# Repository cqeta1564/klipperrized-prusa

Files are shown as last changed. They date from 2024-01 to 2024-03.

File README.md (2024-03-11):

"Buy Me A Coffee" (https://www.buymeacoffee.com/cqeta1564)
# Basic info
This project transforms the original Prusa i3 MK3S+ into a printer running Klipper. The user interface is Mainsail. This mod is safe unless you play with the config. This mod is also not permanent. More information on [how to get back](https://github.com/cqeta1564/klipperrized-prusa/blob/main/README.md#how-to-get-back-to-the-original-firmware).

What you will get from doing this modification to your printer. Faster prints, better quality, and quieter operations.

# Tutorial

## Hardware needed
- The best option is to use a Raspberry Pi Zero (2W preferred), but if you prefer Raspberry Pi 2/3/4/5 can also be used with a bit more work and a few more wires
- If using Raspberry Pi Zero, you'll need [male headers](https://amzn.to/3XND883) so it can mount directly to the Einsy board
- Micro-USB to USB-B (printer cable) or a micro-USB adapter if you already have a USB-B cable

## Pre-Check
- Get the Z offset value from your current firmware (Menu -> Calibration -> Z-offset)

## Installing Mainsail on your Raspberry Pi
1. Download [Pi Imager](https://downloads.raspberrypi.org/imager/imager_latest.exe), install it, and open it

2. 
	a. Select the right board that you are using

	b. Select "Choose OS" > "Other specific-purpose OS" > "3D Printing" > "Mainsail OS" > select the 32-bit version

 	c. Select "Choose Storage" > select the SD card that you want to flash

	d. Select "Next" > "Edit Settings"

	e. In "General" tick "Set username and password" and fill it out

	f. In "General" tick "Configure wireless LAN" if you plan on using wifi and fill it out

	g. In "General" tick "Set locale settings" and fill it out

	h. In "Services" tick "Enable SSH" and choose "Use password authentication"

	i. Click "Save" > "Yes"

3. For Pi Zero users, solder the headers onto the Pi per [Prusa's official instructions](https://help.prusa3d.com/en/article/raspberry-pi-zero-w-preparation-and-installation_2180), but do not plug it into the Einsy board yet

4. Power off your printer and plug in your Pi to the Einsy board per [Prusa's official instructions](https://help.prusa3d.com/en/article/raspberry-pi-zero-w-preparation-and-installation_2180), or power it with a micro USB

5. Power on your printer and navigate to "yourHostName".local/ or IP address of your Pi

6. Navigate to the "Machine" tab and scroll down to "Update Manager". If you see a lot of red buttons that say "invalid" or "error", then give the board 5 minutes and then reboot the board using the power button in the top right corner of the Mainsail interface

7. Navigate back to the update manager, and if the buttons are still red, then wait about 5 minutes. They will eventually populate. There will be a button at the bottom that says "Update All Components" Click this to update all packages to the latest

8. Reboot the Pi again

9. In the "Machine" tab, upload "printer.cfg" from my GitHub

## Flashing Einsy and Setting up Communications between Rpi and Einsy
1. Power down your Pi in Mainsail. If your Pi is plugged into your printer, power that down too and remove the Pi. Connect the USB power source to the micro-USB port on the furthest edge of the board labelled "PWR IN". Plug your micro-USB to USB-b cable in the centre micro-USB port labelled "USB", and then plug the other end into your Einsy mainboard. Turn your printer on if it isn't already.

2. To flash Klipper onto your Einsy

a. Download [Putty](https://www.chiark.greenend.org.uk/~sgtatham/putty/latest.html) and connect to your Pi. Enter the following commands  

   ```yml
   cd ~/klipper/
   make menuconfig   
   ```
   
Compile the firmware for "AVR" "atmega2560". To connect your Pi Zero over serial, select "Enable extra low-level configuration options" and select **UART1** (the RasPi serial) or **UART0** when you plan to connect via the USB.
   Press "q" and exit

   ```yml
   make
   ```

b. find the port for the USB cable

   ```yml
   ls /dev/serial/by-id/*
   ```

Putty will return something like "/dev/serial/by-id/usb-1a86_USB2.0-Serial-if00-port0" or "/dev/serial/by-id/usb-Prusa_Research__prusa3d.com__Original_Prusa_i3_MK3_CZPX4820X004XK35533-if00"
	
Copy this line and replace the corresponding line in the code below. Then run those commands in Putty
	
   ```yml
   sudo service klipper stop
   make flash FLASH_DEVICE=/dev/serial/by-id/usb-1a86_USB2.0-Serial-if00-port0
   sudo service klipper start
   ```

3. Restart the printer by turning the power supply off and on againg
   
4. Ready to print

## How to use PrusaSlicer profiles
You can download profile.ini bundle but be aware that it wont be up to date with newest PrusaSlicer configs. You can also configure your own profile by this tutorial below:

Use profile for Original Prusa MK3.5 Input Shaper with "Print Settings" > "Advanced"  > "Arc fitting" turned off and set "G-code resolution to 0.006. In "Printer Settings" > "General" set "G-code flavor" to "Klipper" and "G-code thumbnail" to "64x64/PNG, 400x300/PNG" and turn off "Supports binary G-code". In "Custom G-code" set "Start G-code" to this: 
```yml
G90 ; use absolute coordinates
M83 ; extruder relative mode

M140 S[first_layer_bed_temperature] ; set bed temp
M104 S170 ; set extruder temp for bed leveling
M109 S170 ; wait for temp
M190 S[first_layer_bed_temperature] ; wait for bed temp

G28 ; home all

BED_MESH_CALIBRATE AREA_START={first_layer_print_min[0]},{first_layer_print_min[1]} AREA_END={first_layer_print_max[0]},{first_layer_print_max[1]}

; prepare for purge
M104 S{first_layer_temperature[0]}
G0 X0 Y-4 Z15 F4800 ; move away and ready for the purge
M109 S{first_layer_temperature[0]}

; Extrude purge line

G92 E0 ; reset extruder position
G0 E7 X15 Z0.2 F500 ; purge
G0 X25 E4 F500 ; purge
G0 X35 E4 F650 ; purge
G0 X45 E4 F800 ; purge
G0 X{45 + 3} Z0.05 F8000 ; wipe, move close to the bed
G0 X{45 + 3 * 2} Z0.2 F8000 ; wipe, move quickly away from the bed

G92 E0
M221 S100 ; reset flow to 100%
```

And "End G-code" to this:
```yml
{if layer_z < max_print_height}G1 Z{z_offset+min(layer_z+1, max_print_height)} F720 ; Move print head up{endif}
M104 S0 ; turn off temperature
M140 S0 ; turn off heatbed
M107 ; turn off fan
G1 X241 Y201 F3600 ; park
{if layer_z < max_print_height}G1 Z{z_offset+min(layer_z+23, max_print_height)} F300 ; Move print head up{endif}
G4 ; wait
M572 S0 ; reset PA
M84 X Y E ; disable motors
; max_layer_z = [max_layer_z]
```

And "Before layer change G-code" to this:
```yml
;BEFORE_LAYER_CHANGE
G92 E0.0
;[layer_z]
M201 X{interpolate_table(extruded_weight_total, (0,4000), (1400,2500), (10000,2500))} Y{interpolate_table(extruded_weight_total, (0,4000), (1400,2500), (10000,2500))}
```

That is all for the fast mk3.5 profile or you can just use slow and old profile for Original Prusa i3 MK3S & MK3S+ with these modifications:

In "Printer Settings" > "General" set "G-code flavor" to "Klipper" and "G-code thumbnail" to "64x64/PNG, 400x300/PNG". In "Custom G-code" set "Start G-code" to this: 

```yml
G90 ; use absolute coordinates
M83 ; extruder relative mode
M140 S[first_layer_bed_temperature] ; set bed temp
M190 S[first_layer_bed_temperature] ; wait for bed temp
G28 W ; home all without mesh bed level
BED_MESH_CALIBRATE AREA_START={first_layer_print_min[0]},{first_layer_print_min[1]} AREA_END={first_layer_print_max[0]},{first_layer_print_max[1]}
{if filament_settings_id[initial_tool]=~/.*Prusament PA11.*/}
G1 Z0.3 F720
G1 Y-3 F1000 ; go outside print area
M104 S[first_layer_temperature] ; set extruder temp
M109 S[first_layer_temperature] ; wait for extruder temp
G92 E0
G1 X60 E9 F1000 ; intro line
G1 X100 E9 F1000 ; intro line
{else}
G1 Z0.2 F720
G1 Y-3 F1000 ; go outside print area
M104 S[first_layer_temperature] ; set extruder temp
M109 S[first_layer_temperature] ; wait for extruder temp
G92 E0
G1 X60 E9 F1000 ; intro line
G1 X100 E12.5 F1000 ; intro line
{endif}
G92 E0
M221 S{if layer_height<0.075}100{else}95{endif}
```

## Optional things that are nice to have 

### Klipper mesh on the print area only
Just download my PrusaSlicer configuration package and use the provided printer profile to use this feature. The Klipper configuration is already set up with this feature.

### Recalibrating input shaper
More info is comming. In the meantime, here is oficial klipper guide: [Recalibrating input shaper](https://www.klipper3d.org/Resonance_Compensation.html) just for your printer using [ADXl345](https://amzn.to/3XMmTZa)

## How to get back to the original firmware
Just reflash the Einsy with the original firmware using PrusaSlicer, just like you would when upgrading it. You will not lose print statistics because they are stored in memory that is not used by Klipper.

## Sources
- Tutorial: https://github.com/Fail-Fast-V0/klipper-prusa-mk3s/
- The file from which my configuration is based on: https://github.com/tillin9/klipper/blob/patch-2/config/printer-prusa-mk3s-2021.cfg
- Another good configuration: https://lab4450.com/latest-projects/revive-your-prusa-mk3s-with-klipper-2-5-compile-and-flash-klipper/
- Klipper mesh on the print area only install guide: https://gist.github.com/ChipCE/95fdbd3c2f3a064397f9610f915f7d02

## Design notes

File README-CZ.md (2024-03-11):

"Buy Me A Coffee" (https://www.buymeacoffee.com/cqeta1564)
# Základní informace
Tento projekt přeměňuje původní tiskárnu Prusa i3 MK3S+ na tiskárnu se systémem Klipper. Uživatelské rozhraní je Mainsail. Tato modifikace je bezpečná, pokud si nebudete hrát s konfigurací. Tato modifikace také není trvalá. Více informací najdete na stránce [jak se dostat zpět](https://github.com/cqeta1564/klipperrized-prusa/blob/main/README-CZ.md#jak-se-vrátit-k-původnímu-firmwaru).

Co touto úpravou tiskárny získáte. Rychlejší výtisky, lepší kvalitu a tišší provoz.

# Tutorial

## Potřebný hardware
- Nejlepší možností je použít Raspberry Pi Zero (nejlépe 2W), ale pokud dáváte přednost Raspberry Pi 2/3/4/5, lze také použít s trochou více práce a několika dalšími dráty.
- Pokud používáte Raspberry Pi Zero, budete potřebovat [samčí hlavičky](https://amzn.to/3XND883), abyste jej mohli připojit přímo k desce Einsy.
- Micro-USB na USB-B (kabel k tiskárně) nebo adaptér micro-USB, pokud již máte kabel USB-B.

## Pre-Check
- Zjistěte hodnotu posunu Z z aktuálního firmwaru (Menu -> Kalibrace -> Posun Z).

## Instalace systému Mainsail do počítače Raspberry Pi
1. Stáhněte si [Pi Imager](https://downloads.raspberrypi.org/imager/imager_latest.exe), nainstalujte jej a otevřete.

2. 
	a. Vyberte správnou desku, kterou používáte

	b. Vyberte "Zvolit OS" > "Jiný OS pro konkrétní účely" > "3D tisk" > "Mainsail OS" > vyberte 32bitovou verzi.

	 c. Vyberte "Choose Storage" > vyberte kartu SD, kterou chcete flashovat.

	d. Vyberte "Další" > "Upravit nastavení".

	e. V části "Obecné" zaškrtněte políčko "Nastavit uživatelské jméno a heslo" a vyplňte je.

	f. V části "Obecné" zaškrtněte políčko "Konfigurace bezdrátové sítě LAN", pokud plánujete používat wifi, a vyplňte jej.

	g. V části "Obecné" zaškrtněte políčko "Nastavení místního jazyka" a vyplňte jej.

	h. V části "Služby" zaškrtněte políčko "Povolit SSH" a vyberte možnost "Použít ověřování heslem".

	i. Klikněte na "Uložit" > "Ano".

3. Uživatelé Pi Zero připájejte hlavičky na Pi podle [oficiálního návodu Prusa](https://help.prusa3d.com/en/article/raspberry-pi-zero-w-preparation-and-installation_2180), ale ještě je nezapojujte do desky Einsy.

4. Vypněte tiskárnu a připojte počítač Pi k desce Einsy podle [oficiálního návodu Prusa](https://help.prusa3d.com/en/article/raspberry-pi-zero-w-preparation-and-installation_2180) nebo jej napájejte pomocí micro USB.

5. Zapněte tiskárnu a přejděte na adresu "yourHostName".local/ nebo IP adresu vašeho počítače Pi.

6. Přejděte na kartu "Stroj" a přejděte dolů na položku "Správce aktualizací". Pokud se zobrazí spousta červených tlačítek s nápisem "invalid" (neplatné) nebo "error" (chyba), dejte desce 5 minut a poté ji restartujte pomocí tlačítka napájení v pravém horním rohu rozhraní programu Mainsail.

7. Přejděte zpět do správce aktualizací, a pokud jsou tlačítka stále červená, počkejte asi 5 minut. Nakonec se vyplní. V dolní části bude tlačítko s nápisem "Aktualizovat všechny součásti" Kliknutím na něj aktualizujete všechny balíčky na nejnovější verzi.

8. Znovu restartujte počítač Pi

9. Na kartě "Machine" nahrajte soubor "printer.cfg" z mého GitHubu.

## Programování Einsy a nastavení komunikace mezi Rpi a Einsy
1. Vypněte počítač Pi v hlavní plachtě. Pokud je počítač Pi připojen k tiskárně, vypněte i ji a vyjměte počítač Pi. Připojte zdroj napájení USB k portu micro-USB na nejvzdálenějším okraji desky označeném "PWR IN". Zapojte kabel micro-USB na USB-b do prostředního portu micro-USB označeného "USB" a druhý konec připojte k základní desce Einsy. Zapněte tiskárnu, pokud ještě není zapnutá.

2. Flashování softwaru Klipper na zařízení Einsy

a. Stáhněte si [Putty](https://www.chiark.greenend.org.uk/~sgtatham/putty/latest.html) a připojte se k počítači Pi. Zadejte následující příkazy  

   ```yml
   cd ~/klipper/
   make menuconfig   
   ```
   
Zkompilujte firmware pro "AVR" "atmega2560". Chcete-li připojit Pi Zero přes sériové rozhraní, vyberte možnost "Enable extra low-level configuration options" (Povolit další nízkoúrovňové konfigurační možnosti) a vyberte **UART1** (sériové rozhraní RasPi) nebo **UART0**, pokud se plánujete připojit přes USB.
   Stiskněte tlačítko "q" a ukončete

   ```yml
   make
   ```

b. najděte port pro kabel USB

   ```yml
   ls /dev/serial/by-id/*
   ```

Putty vrátí něco jako "/dev/serial/by-id/usb-1a86_USB2.0-Serial-if00-port0" nebo "/dev/serial/by-id/usb-Prusa_Research__prusa3d.com__Original_Prusa_i3_MK3_CZPX4820X004XK35533-if00".
	
Zkopírujte tento řádek a nahraďte jím odpovídající řádek v níže uvedeném kódu. Poté spusťte tyto příkazy v programu Putty
	
   ```yml
   sudo service klipper stop
   make flash FLASH_DEVICE=/dev/serial/by-id/usb-1a86_USB2.0-Serial-if00-port0
   sudo service klipper start
   ```

3. Restartujte tiskárnu vypnutím a opětovným zapnutím napájení.
   
4. Připraveno k tisku

## Jak používat profily PrusaSlicer
Můžete si stáhnout balíček profile.ini, ale počítejte s tím, že nebude aktuální s nejnovější konfigurací PrusaSliceru. Můžete si také nakonfigurovat vlastní profil podle tohoto návodu níže:

Použijte profil Original Prusa MK3.5 Input Shaper s vypnutým "Nastavení tisku" > "Pokročilé" > "Přizpůsobení obloukem" a nastavte "G-code rozlišení" na 0.006. V "Nastavení tiskárny" > "Obecné" nastavte "Druh G-code" na "Klipper" a "Náhledy G-codu" na "64x64/PNG, 400x300/PNG" a vypněte "Podpora binárního G-code". V části "Vlastní G-code" nastavte "Začátek G-code" na tuto hodnotu: 
```yml
G90 ; use absolute coordinates
M83 ; extruder relative mode

M140 S[first_layer_bed_temperature] ; set bed temp
M104 S170 ; set extruder temp for bed leveling
M109 S170 ; wait for temp
M190 S[first_layer_bed_temperature] ; wait for bed temp

G28 ; home all

BED_MESH_CALIBRATE AREA_START={first_layer_print_min[0]},{first_layer_print_min[1]} AREA_END={first_layer_print_max[0]},{first_layer_print_max[1]}

; prepare for purge
M104 S{first_layer_temperature[0]}
G0 X0 Y-4 Z15 F4800 ; move away and ready for the purge
M109 S{first_layer_temperature[0]}

; Extrude purge line

G92 E0 ; reset extruder position
G0 E7 X15 Z0.2 F500 ; purge
G0 X25 E4 F500 ; purge
G0 X35 E4 F650 ; purge
G0 X45 E4 F800 ; purge
G0 X{45 + 3} Z0.05 F8000 ; wipe, move close to the bed
G0 X{45 + 3 * 2} Z0.2 F8000 ; wipe, move quickly away from the bed

G92 E0
M221 S100 ; reset flow to 100%
```

A "Konec G-code" na tuto:
```yml
{if layer_z < max_print_height}G1 Z{z_offset+min(layer_z+1, max_print_height)} F720 ; Move print head up{endif}
M104 S0 ; turn off temperature
M140 S0 ; turn off heatbed
M107 ; turn off fan
G1 X241 Y201 F3600 ; park
{if layer_z < max_print_height}G1 Z{z_offset+min(layer_z+23, max_print_height)} F300 ; Move print head up{endif}
G4 ; wait
M572 S0 ; reset PA
M84 X Y E ; disable motors
; max_layer_z = [max_layer_z]
```

A "G-code před změnou vrstvy" na toto:
```yml
;BEFORE_LAYER_CHANGE
G92 E0.0
;[layer_z]
M201 X{interpolate_table(extruded_weight_total, (0,4000), (1400,2500), (10000,2500))} Y{interpolate_table(extruded_weight_total, (0,4000), (1400,2500), (10000,2500))}
```

To je vše pro rychlý profil mk3.5 nebo můžete použít jen pomalý a starý profil pro Original Prusa i3 MK3S & MK3S+ s těmito úpravami:

V "Nastavení tiskárny" > "Obecné" nastavte "Druh G-code" na "Klipper" a "Náhledy G-codu" na "64x64/PNG, 400x300/PNG". V části "Vlastní G-code" nastavte "Začátek G-code" na tuto hodnotu: 
```yml
G90 ; use absolute coordinates
M83 ; extruder relative mode
M140 S[first_layer_bed_temperature] ; set bed temp
M190 S[first_layer_bed_temperature] ; wait for bed temp
G28 W ; home all without mesh bed level
BED_MESH_CALIBRATE AREA_START={first_layer_print_min[0]},{first_layer_print_min[1]} AREA_END={first_layer_print_max[0]},{first_layer_print_max[1]}
{if filament_settings_id[initial_tool]=~/.*Prusament PA11.*/}
G1 Z0.3 F720
G1 Y-3 F1000 ; go outside print area
M104 S[first_layer_temperature] ; set extruder temp
M109 S[first_layer_temperature] ; wait for extruder temp
G92 E0
G1 X60 E9 F1000 ; intro line
G1 X100 E9 F1000 ; intro line
{else}
G1 Z0.2 F720
G1 Y-3 F1000 ; go outside print area
M104 S[first_layer_temperature] ; set extruder temp
M109 S[first_layer_temperature] ; wait for extruder temp
G92 E0
G1 X60 E9 F1000 ; intro line
G1 X100 E12.5 F1000 ; intro line
{endif}
G92 E0
M221 S{if layer_height<0.075}100{else}95{endif}
```

## Nepovinné věci, které je dobré mít

### Klipper mesh pouze v oblasti tisku
Stačí si stáhnout můj konfigurační balíček PrusaSlicer a použít dodaný profil tiskárny, abyste mohli tuto funkci používat. Konfigurace Klipperu je již s touto funkcí nastavena.

### Překalibrování input shaperu
Další informace se chystají. Mezitím je zde oficiální průvodce klipperem: [Překalibrování input shaperu](https://www.klipper3d.org/Resonance_Compensation.html) právě pro vaši tiskárnu pomocí [ADXl345](https://amzn.to/3XMmTZa)

## Jak se vrátit k původnímu firmwaru
Stačí přeflashovat Einsy původním firmwarem pomocí PrusaSlicer, stejně jako při aktualizaci. O tiskové statistiky nepřijdete, protože jsou uloženy v paměti, kterou Klipper nepoužívá.

## Zdroje
- Výukový kurz: https://github.com/Fail-Fast-V0/klipper-prusa-mk3s/
- Soubor, ze kterého vychází moje konfigurace: https://github.com/tillin9/klipper/blob/patch-2/config/printer-prusa-mk3s-2021.cfg
- Další dobrá konfigurace: https://lab4450.com/latest-projects/revive-your-prusa-mk3s-with-klipper-2-5-compile-and-flash-klipper/
- Síťka Klipper pouze v oblasti tisku Návod k instalaci: https://gist.github.com/ChipCE/95fdbd3c2f3a064397f9610f915f7d02

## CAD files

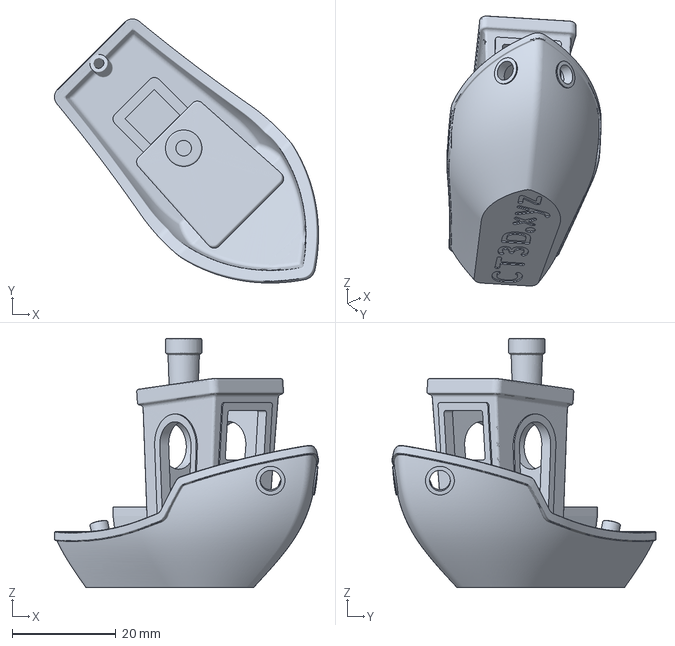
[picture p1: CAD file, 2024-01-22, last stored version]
G2G3TURNEDOFF3dbenchy.3mf
50.8 x 50.8 x 48.0 mm

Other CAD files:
FASTEST3dbenchy.3mf

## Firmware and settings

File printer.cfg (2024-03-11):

# This file contains pin mappings and reasonable defaults for Prusa i3 MK3S
# printers. It will work with MK3 (non-S) by selecting the alternative filament
# sensor. References to common community mods are included as well.
#
# Note: The Einsy boards sold by Prusa have defective firmware on the
# usb-to-serial chip that makes the boards unusable with Klipper through USB.
# While flashing Klipper firmware must be done over USB, the board can be used
# via serial with no additional modification.


# ================================
# =            SENSORS           =
# ================================
[temperature_sensor PC]
sensor_type: temperature_host
min_temp: 10
max_temp: 80

[temperature_sensor einsy_board]
sensor_pin: PF6
sensor_type: TDK NTCG104LH104JT1
min_temp: -10
max_temp: 70

#[temperature_sensor enclosure_temp]
#sensor_type: BME280
#i2c_mcu: host
#min_temp: -20
#max_temp: 120

#[adxl345]
#cs_pin: host:PB2

#[resonance_tester]
#accel_chip: adxl345
#probe_points:
#    125, 105, 20  # an example

[probe]
pin: PB4
x_offset: 24
y_offset: 5
#z_offset: 0
speed: 10.0
samples: 3 #Sampling, primarily for bed mesh. 3 is fine for normal PINDA probes.
samples_result: average
#sample_retract_dist: 1.0 #zkopirovano z druhyho configu, neni za potrebi, ale muze se hodit


# ================================
# =           STEPPERS           =
# ================================
[input_shaper]
shaper_freq_x: 58.0         #61.4  38.6  55.2  53.4      52.6
shaper_freq_y: 64.8         #39.2  44.4  33.6  57.6      56.8
shaper_type_x: ei           #zv    mzv   ei    2hump_ei  3hump_ei
shaper_type_y: 2hump_ei     #zv    mzv   ei    2hump_ei  3hump_ei

[stepper_x]
step_pin: PC0
dir_pin: !PL0
enable_pin: !PA7
#Step distances for common configurations, 16 tooth and 1.8 degree is Prusa.stock, but many people have 0.9 degree steppers to remove VFAs.
#step_distance: .01 #16 pin tooth wheel, 1.8 degree stepper.
#step_distance: .0125 #20 tooth drive wheel, 1.8 degree stepper.
#step_distance: 0.00625 #20 tooth drive wheel. 0.9 degree stepper.
#step_distance: .005 #16 tooth drive wheel, 0.9 degree stepper.
endstop_pin: tmc2130_stepper_x:virtual_endstop
position_endstop: 0
position_max: 250
homing_speed: 50
homing_retract_dist: 0
rotation_distance: 32
microsteps: 16

[tmc2130 stepper_x]
cs_pin: PG0
interpolate: True
run_current: .281738 #.281738
hold_current: .281738 #.281738
sense_resistor: 0.220
diag1_pin: !PK2
driver_IHOLDDELAY: 8
driver_TPOWERDOWN: 0
driver_TBL: 2
driver_TOFF: 3
driver_HEND: 1
driver_HSTRT: 5
driver_PWM_FREQ: 2
driver_PWM_GRAD: 2
driver_PWM_AMPL: 230
driver_PWM_AUTOSCALE: True
driver_SGT: 3

[stepper_y]
step_pin: PC1
dir_pin: PL1
enable_pin: !PA6
#Step distances for common configurations, 16 tooth and 1.8 degree is Prusa.stock, but many people have 0.9 degree steppers to remove VFAs.
#step_distance: .01 #16 pin tooth wheel, 1.8 degree stepper.
#step_distance: .0125 #20 tooth drive wheel, 1.8 degree stepper.
#step_distance: 0.00625 #20 tooth drive wheel. 0.9 degree stepper.
#step_distance: .005 #16 tooth drive wheel, 0.9 degree stepper.
endstop_pin: tmc2130_stepper_y:virtual_endstop
position_endstop: -4
position_max: 210
position_min: -4
homing_speed: 50
homing_retract_dist: 0
rotation_distance: 32
microsteps: 16

[tmc2130 stepper_y]
cs_pin: PG2
interpolate: True
run_current: .3480291 #.281738
hold_current: .3480291 #.281738
#Run at the same current as X-axis for lower noise, and to keep steppers cooler.
#This should work, but if Y starts skipping steps, you may need to bump up to Prusa stock.
#run_current: .3480291
#hold_current: .3480291
sense_resistor: 0.220
diag1_pin: !PK7
driver_IHOLDDELAY: 8
driver_TPOWERDOWN: 0
driver_TBL: 2
driver_TOFF: 3
driver_HEND: 1
driver_HSTRT: 5
driver_PWM_FREQ: 2
driver_PWM_GRAD: 2
#driver_PWM_AMPL: 235
driver_PWM_AMPL: 230
driver_PWM_AUTOSCALE: True
driver_SGT: 3

[stepper_z]
step_pin: PC2
dir_pin: !PL2
enable_pin: !PA5
#step_distance: .0025
endstop_pin: probe:z_virtual_endstop
#Please update the Z height in the Tram_Z macro below.
position_max: 200 #This is the MK3S default.
#position_max: 210 #Use this for a stock MK3 non-S, BMG, or Bear extruders for the MK3S.
position_min: -2
homing_speed: 13.333
rotation_distance: 8
microsteps: 16

[tmc2130 stepper_z]
cs_pin: PK5
interpolate: True
run_current: .53033
hold_current: .53033
sense_resistor: 0.220
diag1_pin: !PK6
driver_IHOLDDELAY: 8
driver_TPOWERDOWN: 0
driver_TBL: 2
driver_TOFF: 3
driver_HEND: 1
driver_HSTRT: 5
driver_PWM_FREQ: 2
driver_PWM_GRAD: 4
driver_PWM_AMPL: 200
driver_PWM_AUTOSCALE: True
driver_SGT: 4

[extruder]
step_pin: PC3
dir_pin: PL6
enable_pin: !PA4
#step_distance: .0035714 #Stock Prusa or Bear extruder.
#step_distance: .0012048 #BMG or other 3:1 ratio extruder.
nozzle_diameter: 0.400
filament_diameter: 1.750
# The max extrude cross section is increased for the purge line, but in theory
# its probably a bad idea to have it this large, as its purpose is to catch
# poorly sliced objects that extrude too much for small moves.
max_extrude_cross_section: 500.0
# Allows to load filament and purge up to 500mm
max_extrude_only_distance: 500.0
max_extrude_only_velocity: 120.0
max_extrude_only_accel: 5000.0
heater_pin: PE5
sensor_type: ATC Semitec 104GT-2
sensor_pin: PF0
#control: pid
#pid_Kp: 16.13
#pid_Ki: 1.1625
#pid_Kd: 56.23
min_temp: 0
max_temp: 305
microsteps: 32
rotation_distance: 22.85696
full_steps_per_rotation: 200
pressure_advance: 0.0 # Do not set, prusaslicer has a nice tool and with combination of gcode macro sets PA automatically

[tmc2130 extruder]
cs_pin: PK4
interpolate: True
run_current: .513757
hold_current: .513757
sense_resistor: 0.220
diag1_pin: !PK3
driver_IHOLDDELAY: 8
driver_TPOWERDOWN: 0
driver_TBL: 2
driver_TOFF: 3
driver_HEND: 1
driver_HSTRT: 5
driver_PWM_FREQ: 2
driver_PWM_GRAD: 4
driver_PWM_AMPL: 240
driver_PWM_AUTOSCALE: True
driver_SGT: 3


# ================================
# =        OTHER HARDWARE        =
# ================================
[heater_bed]
heater_pin: PG5
sensor_type: EPCOS 100K B57560G104F
sensor_pin: PF2
#control: pid
#pid_Kp: 126.13
#pid_Ki: 4.3
#pid_Kd: 924.76
min_temp: 0
max_temp: 125

[heater_fan nozzle_cooling_fan]
pin: PH5
heater: extruder
heater_temp: 50.0
fan_speed: 1.0

# Part Cooling Fan
[fan]
pin: PH3

[mcu]
#serial: /dev/serial0  # If you are using internal RPI serial port
serial: /dev/ttyACM0 # If you are using RPI via USB connection to printer
#baud: 256000
restart_method: command

#[mcu host]
#serial: /tmp/klipper_host_mcu

[display]
lcd_type: hd44780
rs_pin: PD5
e_pin: PF7
d4_pin: PF5
d5_pin: PG4
d6_pin: PH7
d7_pin: PG3
encoder_pins: ^PJ1,^PJ2
click_pin: ^!PH6

[output_pin LCD_backlight_pin]
pin: PE3
pwm: True
hardware_pwm: True
value: 0.25 # 30% backlight
shutdown_value: 1 # Back to full backlight (without PWM) on restart
cycle_time: 0.001 # Default 0.1s cycle time flickers as hell

# Keeps Debug LED off / not floating
[static_digital_output debug_led]
pins: !PB7

[output_pin BEEPER_pin]
pin: PH2
pwm: True
value: 0
shutdown_value:0
cycle_time: 0.001
scale: 1000

# These settings are not that important because prusaslicer sets them automatically, which I recommend using
[printer]
kinematics: cartesian
max_velocity: 500
max_accel: 4700
max_accel_to_decel: 2350
max_z_velocity: 50
max_z_accel: 300
square_corner_velocity: 5

#MK3S Filament IR Barrier Sensor.
[filament_switch_sensor fsensor]
pause_on_runout: True
runout_gcode:
    M118 Filament Runout Detected
    M600
insert_gcode:
    M118 Filament Load Detected
    LOAD_FILAMENT
event_delay: 3.0
pause_delay: 0.01
switch_pin: !PK0

#MK3 (non-S) Filament Sensor.
#[pat9125 fsensor]
#pause_on_runout: True
#runout_gcode:
# M118 Filament Runout Detected
#  M600 X250 Y-3 Z10
#insert_gcode:
# M118 Filament Load Detected
#  LOAD_FILAMENT
#invert_axis: True
#oq_enable: True


# ================================
# =        INICIAL CONFIG        =
# ================================
[bed_mesh]
#algorithm: bicubic
#fade_end: 10
#faulty_region_1_max: 120.0, 74.0 
#faulty_region_1_min: 85.0, 45.0 # 103,69
#faulty_region_2_max: 125.0, 165
#faulty_region_2_min: 70, 110 # 103, 137
horizontal_move_z: 4 #was 2
mesh_max: 240,198
mesh_min: 35, 6
mesh_pps: 0,0 #Don't generate interperlated points so our mesh is compatible with nylock calculators like https://pcboy.github.io/g81_relative/
probe_count: 7,7
speed: 200

#Home in lower, lefthand corner.
[homing_override]
gcode:
# G1 Z50
 G28 X0 Y200
 G1 X1 Y0 F5000
# G1 X1 Y200 F5000 #Home vlevo vzadu
# G1 X220 Y0 F5000 #Home vpravo vepredu
 G28 Z0
axes: Z
set_position_x: 0
set_position_y: 0
set_position_z: 0

[respond]
default_type: command

[pause_resume]

[delayed_gcode clear_display]
initial_duration: 0.
gcode:
  M117

[display_status]

[force_move]
enable_force_move: TRUE

[virtual_sdcard]
path: ~/printer_data/gcodes

#If not using with Octoprint remove the menu.
[menu __main __octoprint]
type: disabled

[exclude_object]

[gcode_arcs]
resolution: 0.008
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

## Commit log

2024-01-17 Update printer.cfg
    Added "[exclude_object]" to be able to exclude objects during printing.
    [printer.cfg]
2024-01-17 Added PrusaSlicer profile/config
    This is the PrusaSlicer configuration that is modified for Klipper needs. You can use the other profiles but stick to the modified settings from this one.
2024-01-18 Added mesh on print area only
    Added mesh on print area only by this tutorial: https://gist.github.com/ChipCE/95fdbd3c2f3a064397f9610f915f7d02
    [printer.cfg]
2024-01-18 Fixed z calibration
    Z hop must have been bigger. I changed it from 2 to 4.
    [printer.cfg]
2024-01-18 Added pressure advance
    Added pressure advance. For more information about the configuration, see the readme.
    [printer.cfg]
2024-01-19 Fixed comments
    Translate comments into English.
    [printer.cfg]
2024-01-22 Added color change
    I haven't test it yet, but it looks ok.
    Added color change based on https://www.reddit.com/r/klippers/comments/qxjcq2/need_a_m600_macro/
    [printer.cfg]
2024-01-22 Fast settings... go vruuuum
    Added this 3dbenchy with my fastest settings. It doesn't look nice, but it prints. You can normally use printer.cfg I have on GitHub and get the fastest prints. It's mostly in slicer settings. You may have problem with cooling or klipper shuting down, because of lack of the compute resources. If you want to get the fastest prints, you will need to run klipper from notebook or desktop.
    [FASTEST3dbenchy.3mf]
2024-01-22 I don't have nasa pc :,(
    These settings will probably work without shutting down the system.
    [G2G3TURNEDOFF3dbenchy.3mf]
2024-02-01 Reduced max accel
    Reduced maximum acceleration due to motor skipping.
    [printer.cfg]
2024-03-11 Update printer.cfg
    Added macro for automatic PA and fixed comments
    [printer.cfg]
